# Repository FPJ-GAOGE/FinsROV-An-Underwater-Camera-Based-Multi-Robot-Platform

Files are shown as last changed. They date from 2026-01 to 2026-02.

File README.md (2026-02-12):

## FinsROV: an Underwater Camera-Based Multi-robot platform





FinsROV is a low-cost, open-source Underwater robot platform designed for underwater task and research in robotics and AI. The eight-thruster configuration effectively ensures the flexibility of the robot's omnidirectional movement, and the dual-gimbal platform provides ample hardware expansion space, which can be applied to task scenarios such as underwater object tracking and underwater target recognition. This project supports both Chinese and English languages, though some videos and documents are only available in Chinese (Maybe this is a great opportunity to learn Chinese LOL)

FinsROV是一台开源的低成本水下机器人平台，面向AI和机器人领域中的水下任务和研究针对性设计。八推进器结构有效的保证了机器人全向运动的的灵活性，双云台平台提供了充足的硬件扩展空间，可以运用于水下物体跟踪，水下目标识别等任务场景。本项目提供中英两种语言的支持，但部分视频和文件仅有中文支持

## Overview

The FinsROV consists of a waterproof compartment with its internal circuitry, 8 propellers, 4 servos, 4 water depth sensors, and various brackets in total, with the model shown as follows:

FinsROV整体包含防水仓及其内部电路、推进器 x8、舵机 x4、水深传感器 x4以及各个支架，模型如下：
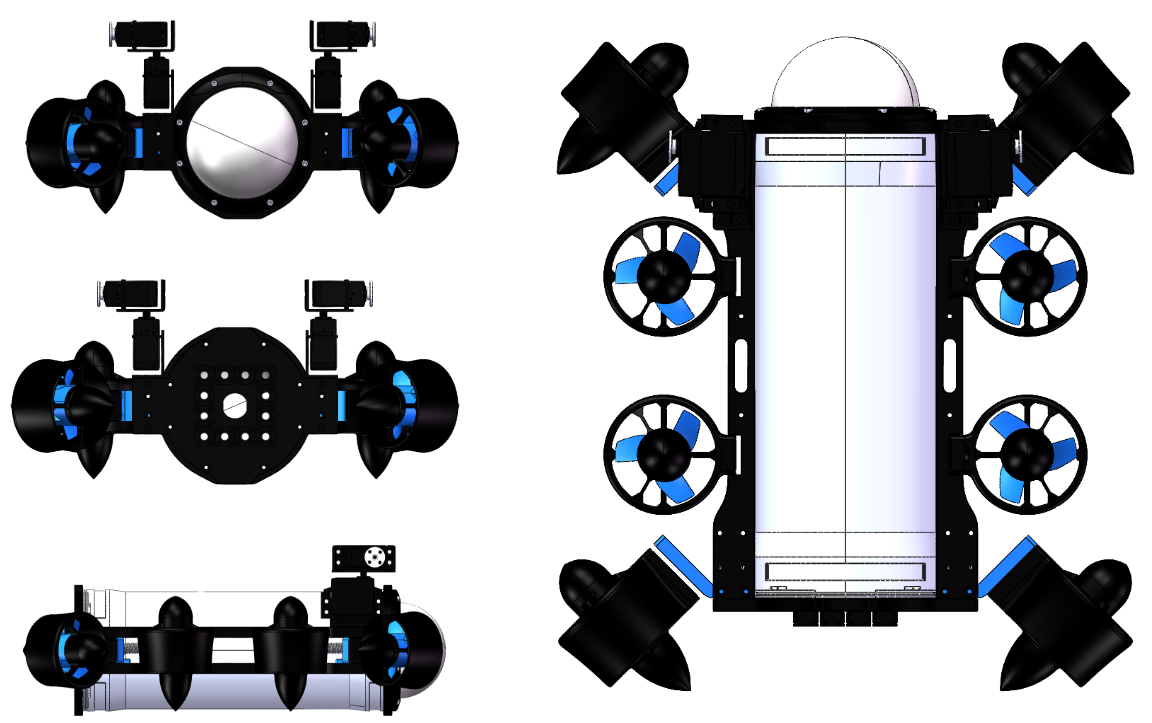
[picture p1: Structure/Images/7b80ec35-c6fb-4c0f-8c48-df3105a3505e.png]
Model


FinsROV is equipped with two 2-DOF gimbals mounted on either side of the submersible respectively. Each gimbal consists of two servos, with a maximum rotation angle of -90° to 90° for each servo.

FinsROV配置了两个二自由度的云台、分别置于潜器的两侧，一个云台由两个舵机组成，每个舵机的最大旋转角度为（-90°~90°）


We have open-sourced all structural components of the underwater robot, which can be found in the [Structure](https://github.com/FPJ-GAOGE/FinsROV-An-Underwater-Camera-Based-Multi-Robot-Platform/tree/main/Structure) folder, with the corresponding STEP files provided. The robot’s structure can be modified using software such as Solidworks, and the relevant structural components can be manufactured by means including 3D printing and CNC machining. We welcome everyone to upgrade and modify this robot platform.

我们开源了水下机器人所有的结构件，在[Structure](https://github.com/FPJ-GAOGE/FinsROV-An-Underwater-Camera-Based-Multi-Robot-Platform/tree/main/Structure)文件夹中，提供对应的STEP文件，通过Solidworks等软件，可以对机器人结构进行修改。通过3D打印或者CNC加工等不同的形式，都可以制造对应的结构件，我们欢迎大家对机器人平台进行升级和改造

## Parameters

<table style="width:100%; border-collapse: collapse;">
  <thead>
    <tr style="border: 1px solid #ddd;">
      <th style="border: 1px solid #ddd; padding: 8px; text-align: left;">Category</th>
      <th style="border: 1px solid #ddd; padding: 8px; text-align: left;">Sub-item</th>
      <th style="border: 1px solid #ddd; padding: 8px; text-align: left;">Parameter</th>
      <th style="border: 1px solid #ddd; padding: 8px; text-align: left;">Supplementary Note</th>
    </tr>
  </thead>
  <tbody>
    <tr style="border: 1px solid #ddd;">
      <td rowspan="4" style="border: 1px solid #ddd; padding: 8px; background-color: #f5f5f5;"><strong>Specifications</strong></td>
      <td style="border: 1px solid #ddd; padding: 8px;">Dimensions (Length × Width × Height)</td>
      <td style="border: 1px solid #ddd; padding: 8px;">40cm*35cm*15cm</td>
      <td style="border: 1px solid #ddd; padding: 8px;">-</td>
    </tr>
    <tr style="border: 1px solid #ddd;">
      <td style="border: 1px solid #ddd; padding: 8px;">Power & Endurance Time</td>
      <td style="border: 1px solid #ddd; padding: 8px;">Approx. 13.75W, Approx. 2h</td>
      <td style="border: 1px solid #ddd; padding: 8px;">Adapted to RC model batteries with xt30/60 interface</td>
    </tr>
    <tr style="border: 1px solid #ddd;">
      <td style="border: 1px solid #ddd; padding: 8px;">Weight in Air</td>
      <td style="border: 1px solid #ddd; padding: 8px;">4.85Kg</td>
      <td style="border: 1px solid #ddd; padding: 8px;">-</td>
    </tr>
    <tr style="border: 1px solid #ddd;">
      <td style="border: 1px solid #ddd; padding: 8px;">Operating Depth</td>
      <td style="border: 1px solid #ddd; padding: 8px;">10-20m (Passed internal pressure test)</td>
      <td style="border: 1px solid #ddd; padding: 8px;">Passed internal pressure test</td>
    </tr>
    <tr style="border: 1px solid #ddd;">
      <td rowspan="6" style="border: 1px solid #ddd; padding: 8px; background-color: #f5f5f5;"><strong>Power System</strong></td>
      <td style="border: 1px solid #ddd; padding: 8px;">Maximum Acceleration in Still Water</td>
      <td style="border: 1px solid #ddd; padding: 8px;">4.6m/s²</td>
      <td style="border: 1px solid #ddd; padding: 8px;">-</td>
    </tr>
    <tr style="border: 1px solid #ddd;">
      <td style="border: 1px solid #ddd; padding: 8px;">Maximum Speed in Still Water</td>
      <td style="border: 1px solid #ddd; padding: 8px;">Approx. 3m/s</td>
      <td style="border: 1px solid #ddd; padding: 8px;">-</td>
    </tr>
    <tr style="border: 1px solid #ddd;">
      <td style="border: 1px solid #ddd; padding: 8px;">Maximum Angular Velocity of Steering in Still Water</td>
      <td style="border: 1px solid #ddd; padding: 8px;">5.7rad/s</td>
      <td style="border: 1px solid #ddd; padding: 8px;">-</td>
    </tr>
    <tr style="border: 1px solid #ddd;">
      <td style="border: 1px solid #ddd; padding: 8px;">Control Frequency</td>
      <td style="border: 1px solid #ddd; padding: 8px;">150Hz</td>
      <td style="border: 1px solid #ddd; padding: 8px;">Can be adjusted according to actual needs</td>
    </tr>
    <tr style="border: 1px solid #ddd;">
      <td style="border: 1px solid #ddd; padding: 8px;">Baud Rate</td>
      <td style="border: 1px solid #ddd; padding: 8px;">115200</td>
      <td style="border: 1px solid #ddd; padding: 8px;">-</td>
    </tr>
    <tr style="border: 1px solid #ddd;">
      <td style="border: 1px solid #ddd; padding: 8px;">Load Capacity</td>
      <td style="border: 1px solid #ddd; padding: 8px;">10-15N</td>
      <td style="border: 1px solid #ddd; padding: 8px;">-</td>
    </tr>
  </tbody>
</table>

<table style="width:100%; border-collapse: collapse;">
  <thead>
    <tr style="border: 1px solid #ddd;">
      <th style="border: 1px solid #ddd; padding: 8px; text-align: left;">类别</th>
      <th style="border: 1px solid #ddd; padding: 8px; text-align: left;">子项</th>
      <th style="border: 1px solid #ddd; padding: 8px; text-align: left;">参数</th>
      <th style="border: 1px solid #ddd; padding: 8px; text-align: left;">补充说明</th>
    </tr>
  </thead>
  <tbody>
    <tr style="border: 1px solid #ddd;">
      <td rowspan="4" style="border: 1px solid #ddd; padding: 8px; background-color: #f5f5f5;"><strong>规格</strong></td>
      <td style="border: 1px solid #ddd; padding: 8px;">尺寸（长×宽×高）</td>
      <td style="border: 1px solid #ddd; padding: 8px;">40cm*35cm*15cm</td>
      <td style="border: 1px solid #ddd; padding: 8px;"></td>
    </tr>
    <tr style="border: 1px solid #ddd;">
      <td style="border: 1px solid #ddd; padding: 8px;">功率 续航时间</td>
      <td style="border: 1px solid #ddd; padding: 8px;">约13.75W，约2h</td>
      <td style="border: 1px solid #ddd; padding: 8px;">适配xt30/60接口的航模电池</td>
    </tr>
    <tr style="border: 1px solid #ddd;">
      <td style="border: 1px solid #ddd; padding: 8px;">空气中重量</td>
      <td style="border: 1px solid #ddd; padding: 8px;">4.85Kg</td>
      <td style="border: 1px solid #ddd; padding: 8px;"></td>
    </tr>
    <tr style="border: 1px solid #ddd;">
      <td style="border: 1px solid #ddd; padding: 8px;">作业深度</td>
      <td style="border: 1px solid #ddd; padding: 8px;">10-20m，已通过内压测试</td>
      <td style="border: 1px solid #ddd; padding: 8px;">已通过内压测试</td>
    </tr>
    <tr style="border: 1px solid #ddd;">
      <td rowspan="6" style="border: 1px solid #ddd; padding: 8px; background-color: #f5f5f5;"><strong>动力系统</strong></td>
      <td style="border: 1px solid #ddd; padding: 8px;">静水航行最大加速度</td>
      <td style="border: 1px solid #ddd; padding: 8px;">4.6m/s^2</td>
      <td style="border: 1px solid #ddd; padding: 8px;"></td>
    </tr>
    <tr style="border: 1px solid #ddd;">
      <td style="border: 1px solid #ddd; padding: 8px;">静水航行最大速度</td>
      <td style="border: 1px solid #ddd; padding: 8px;">约3m/s</td>
      <td style="border: 1px solid #ddd; padding: 8px;"></td>
    </tr>
    <tr style="border: 1px solid #ddd;">
      <td style="border: 1px solid #ddd; padding: 8px;">静水转向最大角速度</td>
      <td style="border: 1px solid #ddd; padding: 8px;">5.7rad/s</td>
      <td style="border: 1px solid #ddd; padding: 8px;"></td>
    </tr>
    <tr style="border: 1px solid #ddd;">
      <td style="border: 1px solid #ddd; padding: 8px;">控制频率</td>
      <td style="border: 1px solid #ddd; padding: 8px;">150Hz</td>
      <td style="border: 1px solid #ddd; padding: 8px;">可以根据实际需要进行调整</td>
    </tr>
    <tr style="border: 1px solid #ddd;">
      <td style="border: 1px solid #ddd; padding: 8px;">波特率</td>
      <td style="border: 1px solid #ddd; padding: 8px;">115200</td>
      <td style="border: 1px solid #ddd; padding: 8px;"></td>
    </tr>
    <tr style="border: 1px solid #ddd;">
      <td style="border: 1px solid #ddd; padding: 8px;">载荷</td>
      <td style="border: 1px solid #ddd; padding: 8px;">10-15N</td>
      <td style="border: 1px solid #ddd; padding: 8px;"></td>
    </tr>
  </tbody>
</table>

## BOM

The complete BOM of our robot is shown below. For regions where components can be directly purchased on Taobao, you may click the links directly (this is not an advertisement; you may purchase from other suppliers). For those with no access to Taobao, please refer to the following information. A downloadable version of the BOM is also available in the Structure folder.

我们机器人的完整BOM表格如下，对于能够直接通过淘宝采购零部件的地区，可以直接点击链接参考（不涉及任何广告，仅供参考）。在Structure文件中也有对应可下载的BOM文件。

[中文版本](https://docs.google.com/spreadsheets/d/1fIgdKPsx-9QTdMGvk-Vg6hmxgAVsjg4v-JMBh90Yp5g/edit?gid=0#gid=0)

[English Version BOM](https://docs.google.com/spreadsheets/d/1fIgdKPsx-9QTdMGvk-Vg6hmxgAVsjg4v-JMBh90Yp5g/edit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)

## Controller

All controller codes are stored in the [Lower level controller](https://github.com/FPJ-GAOGE/FinsROV-An-Underwater-Camera-Based-Multi-Robot-Platform/tree/main/Code/Lower_Level_Controller) and can be used with the Readme file. In this project, our lower-level controller is based on the DJI Robomaster C-board (STM32F4) and developed with Keil. For secondary development of the code, you need to download Keil Version 5.38 or later, and it depends on the file Keil.STM32F4xx_DFP.2.14.0.pack. Install dpinst_x86.exe (for 32-bit systems) or dpinst_amd64.exe (for 64-bit systems) from the STLink package. The process for wireless programmers is similar to that of wired programmers; simply select CMSIS-DAP Debugger when choosing the debug tool, and there is generally no need to modify the clock frequency. For better performance, we recommend using the [FINEMOTE](https://github.com/FINS-Fines/FineMote) developed by our laboratory (note: some hardware is not yet adapted). It is a powerful embedded development framework that will also be used synchronously in our new-generation underwater robots.

控制器代码在[Lower level controller](https://github.com/FPJ-GAOGE/FinsROV-An-Underwater-Camera-Based-Multi-Robot-Platform/tree/main/Code/Lower_Level_Controller)文件夹中，配合Readme使用，本项目中我们的下位机是基于DJI Robomaster C板（STM32F4），使用Keil进行开发的。如果需要对代码进行二次开发，需要下载Keil 5.38以上版本。依赖Keil.STM32F4xx_DFP.2.14.0.pack文件。安装stlink中的dpinst_x86.exe（32位）或 dpinst_amd64.exe（64位）。无线烧写器与有线烧写器流程类似，在选择调试工具的时候改为选择CMSIS-DAP Debugger即可，一般不需要修改时钟频率。如果你想有更好的性能，推荐使用我们实验室开发的[FINEMOTE框架](https://github.com/FINS-Fines/FineMote)（部分硬件暂未适配），这是一种强大的嵌入式开发框架，我们新一代的水下机器人上也会同步使用该框架

## Wired-Joystick

Our robot platform supports a variety of host computer systems, including but not limited to Windows, Linux, macOS, Android, Raspberry Pi, etc. We recommend using a game Joystick for control. The relevant code is available in [Joystick_Control](https://github.com/FPJ-GAOGE/FinsROV-An-Underwater-Camera-Based-Multi-Robot-Platform/tree/main/Code/Joystick_Control) and should be used in conjunction with the Readme file.

我们的机器人平台支持多种上位机系统，包括但不限于windows，linux，Mac os，Android，树莓派等，我们推荐使用手柄进行控制。相关代码在[Joystick_Control](https://github.com/FPJ-GAOGE/FinsROV-An-Underwater-Camera-Based-Multi-Robot-Platform/tree/main/Code/Joystick_Control)中，配合Readme使用

## Education

We provide a complete set of video tutorials for building the underwater vehicle. We sincerely apologize that these tutorials are only available on Bilibili with Chinese voice-overs and subtitles. We will also upload other relevant content, and we welcome you to subscribe to our [channel](https://space.bilibili.com/1188256336?spm_id_from=333.40164.0.0). Additionally, the [Making_Instructions](https://github.com/FPJ-GAOGE/FinsROV-An-Underwater-Camera-Based-Multi-Robot-Platform/tree/main/Making_Instructions) folder also contains some documentation on the making instructions.

我们为制作潜器提供完整的视频教程，但是非常抱歉，相关教程上传至BiliBili且只有中文配音与字幕。我们也会上传其他相关的内容，[欢迎订阅](https://space.bilibili.com/1188256336?spm_id_from=333.40164.0.0)。同时，[Making_Instructions](https://github.com/FPJ-GAOGE/FinsROV-An-Underwater-Camera-Based-Multi-Robot-Platform/tree/main/Making_Instructions)中也包含部分制作说明文档。

How to bulid the robot platform & coding: [【上海交通大学】从0-1带你制作水下机器人](https://www.bilibili.com/video/BV13vcvzgEv3?p=11&vd_source=225e86b359e69725bfc871c2685a31c8)

Basic theory about underwater robot: [【面向水下机器人的动力学与运动学建模及控制器分析】](https://www.bilibili.com/video/BV1VXmQBRE2a/?share_source=copy_web&vd_source=898a23397484d4386766c76dfa58679f)

Demo: [【目前可公开的情报：FINS第一代水下机器人】](https://www.bilibili.com/video/BV1oC41177Rn/?share_source=copy_web&vd_source=e6237e17b71511df8920049cd998c076)

## Thank & Citation

This project acknowledges the contributions of Ding Lin, Jisheng Xu, Jiahao Lin, Yanqi Feng, Jiaming Guo and other students who are or have been part of the FINS-Underwater Group.

这个项目要感谢Ding Lin, Jisheng Xu, Jiahao Lin, Yanqi Feng, Jiaming Guo等来自或参与过FINS-Underwater Group的同学的贡献 

If you find this code useful, we would appreciate if you would cite our paper:

如果你觉得我们的开源项目能够帮助到你，欢迎你引用我们的文章！并持续关注我们的后续研究：
```
@article{xu2025aucamp,
  title={Aucamp: An Underwater Camera-Based Multi-Robot Platform with Low-Cost, Distributed, and Robust Localization},
  author={Xu, Jisheng and Lin, Ding and Fong, Pangkit and Fang, Chongrong and Duan, Xiaoming and He, Jianping},
  journal={arXiv preprint arXiv:2506.09876},
  year={2025}
}
```

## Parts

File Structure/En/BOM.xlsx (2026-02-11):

Type | Item Description | Link | Detail | Price(CNY) | Number | Note
Disclaimer | We are not affiliated with or endorse this company in any way. We have not tested or validated the product. Any such offerings are independent of our project.
 | If you are from regions outside mainland China or areas where Taobao e-commerce services are not readily available, you may refer to the BOM specifications to purchase equivalent items through convenient channels, but we cannot guarantee the consistency of the final assembly results. |  |  |  |  |  | The quantity of screws is for reference only; please prepare extra ones.
Essentials
Structure | Rear cabin hatch |  | Custom Aluminum Alloy CNC Machining | 240 | 1 |  | Category | Type | Number
 | Front cabin mount |  |  | 180 | 1 |  | Countersunk Head Hexagon Socket Screw | M3(Head Diameter6)*5 | 20
 | Thruster mount |  |  | 680 | 4 |  |  | M3(Head Diameter6)*10 | 8
 | Horizontal thruster bracket |  |  | 480 | 4 |  |  | M3(Head Diameter8)*8 | 16
 | Cable-passing screw |  |  | 1140 | 12 |  | Cup Head Hexagon Socket Screw | M4*16 | 32
 | Underwater aviation connector | https://item.taobao.com/item.htm?spm=a1z09.2.0.0.18002e8dzucueB&id=619481441943&_u=f2ig9se45843 | 3W 6-Core | 272 | 1 | Send cable directly to supplier for processing. |  | M3*16 | 20
 | Servo connector | https://item.taobao.com/item.htm?id=557166026079&sku_properties=31309:48651884 | Multifunctional Bracket | 18.4 | 4 |  |  | M3*12 | 45
 |  |  | Metal Servo Horn | 10 | 4 |  |  | M3*10 | 8
 | Waterproof compartment | https://item.taobao.com/item.htm?spm=a1z09.2.0.0.ef7d2e8dO2XjuV&id=662343463249&_u=92ig9se46f55 | Cabin Tube & Flange Kit + Hemispherical Cover + Pressure Plate | 515 | 1 |  |  | M2.5*8 | 4
 | Internal bracket of waterproof compartment | 3D打印 |  |  |  |  |  | M2*10 | 48
Electronics | Propeller | https://item.taobao.com/item.htm?spm=a1z09.2.0.0.ef7d2e8dO2XjuV&id=591864716045&_u=92ig9se435ad | 1 Pair of CW/CCW Propellers (Built-in ESC for 4S Voltage) | 2037 | 4 |  |  | M3*4 | 12
 | Servo | LIEYING/QFS2025全防水/潜水/水下机器人舵机全金属外壳IPX68等级-淘宝网 (taobao.com) (https://item.taobao.com/item.htm?_u=i20at7545jacc4&id=680656749408&spm=a1z09.2.0.0.3c6c2e8dmFwRSe) | 20KG (for Underwater Diving) Underwater Robot, 180° (0.5-2.5ms) | 432 | 4 | Custom extended cable, total length 1m. |  | M2.5*4 | 4
 | Water depth sensor | M10 水压水深传感器 高精度 深度传感器 MS5837-30BA 带温度 ROV-淘宝网 (taobao.com) (https://item.taobao.com/item.htm?_u=320at7545j5b4a&id=605375059849&spm=a1z09.2.0.0.2d472e8d3f5Wg1) | Standard Version, Stainless Steel, 10m, Sensor Adapter Board Kit | 1319.6 | 4 | Custom extended cable, total length 60cm. | Single-head Copper Spacer | M3*4+4 | 12
 | I2C expansion board | TCA9548A IIC多路扩展模块 8路I2C通信 I2C开关开发-淘宝网 (https://item.taobao.com/item.htm?id=677595693967&skuId=6126765579570) | Straight/Right-Angle Pin Headers | 10.56 | 1 |  |  | M2.5*4+4 | 4
 | PWM expansion board | 16路PWM Servo 舵机驱动板机器人控制器IIC接口驱动器模块PCA9685-tmall.com天猫 (https://detail.tmall.com/item.htm?_u=m20at7545j0770&id=624960039615&spm=a1z09.2.0.0.570d2e8dWadFaY) | Pre-Soldered | 15 | 1 |  | Hexagonal Single-head Nylon Spacer | M3*70+6 | 6
 | TTL to 422 converter | RS422互转TTL双向信号 全双工422转单片机MAX490转TTL模块-tmall.com天猫 (https://detail.tmall.com/item.htm?_u=q2ig9se4d19b&id=715839278393) |  | 9.1 | 1 |  |  | M3*45+6 | 3
 | 422 to USB converter | 绿联usb转rs485/422/232串口线工业级九针db9针数据调试接口通讯模块芯片连接笔记本和电脑口转接头转换器-tmall.com天猫 (https://detail.tmall.com/item.htm?id=599997955029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) | 1 Piece, Length Customizable | 79 | 1 |  |  | M3*40+6 | 3
 | Wireless debugger | 高速无线调试器DAPLink仿真器STM32编程烧录下载器塔克OpenCTR-淘宝网 (https://item.taobao.com/item.htm?abbucket=8&id=745548099223&ns=1&skuId=5310177214467&xxc=taobaoSearch) | 2 Debuggers + Dupont Cables | 89 | 2 |  | Cap Nut | M3 | 16
 | DJI RoboMaster C-board | ROBOMASTER萝马集市 开发板C型-淘宝网 (taobao.com) (https://item.taobao.com/item.htm?_u=i20at7545j5174&id=611226266955&spm=a1z09.2.0.0.292e2e8d43HZbM) |  | 379 | 1 |  | Hex Nut | M3 | 4
 | Camera |  | Either External Waterproof Camera or Internal Cabin Camera is Acceptable |  | 1 |  | Embedded Nut | M3*4+6 | 4
Others | Cable |  | Custom Zero-Buoyancy Cable: 2p*1mm² Power Cable + 4p Signal Cable
 | Screw |  | See the right table
 | Terminal block | https://item.taobao.com/item.htm?id=562191894078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 | h3802 10P | 25.2 | 2
 |  |  | Chocolate Color [EBL-10-5-Connector], Non-printed | 12.6 | 2
 |  | https://item.taobao.com/item.htm?spm=a1z09.2.0.0.5b912e8dQl5wtC&id=661948958655&_u=h2ig9se4f606 | h3800 12P | 36 | 2
 |  |  | h3800 16P | 24 | 1
 | Terminal block
 | Dupont adapter cable |  | 4P 100mm to Dupont Female SH1.25; 3P 100mm to Dupont Female GH1.25
 | Dupont cable |  | 6-Color Male to Female, 10cm
 | Waterproof gasket | 绿色氟胶O型圈外10.5/11/11.5/12/12.5/13/13.5/14/14.5/15*1.5mm-tmall.com天猫 (https://detail.tmall.com/item.htm?id=680012535670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) | Outer Diameter 12mm*1.5mm |  | 12

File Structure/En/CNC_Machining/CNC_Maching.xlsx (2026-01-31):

Name | Quantity | Material | Remarks
Front_Cabin_Mount | 1 | Al Alloy Anodized Black
Rear_Cabin_Hatch | 1 | Al Alloy Anodized Black | All similar locations here: drill & tap M2 threaded holes, depth 4 mm, Qty. 48
Thruster_Mount | 4 | Al Alloy Anodized Black | All similar locations here: drill & tap M3 threaded holes, depth 10 mm, Qty. 12
Horizontal_Thruster_Bracket | 4 | Al Alloy Anodized Blue | All similar locations here: drill & tap M3 threaded holes, depth 8 mm, Qty. 6
Cable-passing_Screw | 12 | Al Alloy Anodized Black

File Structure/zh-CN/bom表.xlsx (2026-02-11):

类别 | 材料名称 | 购买链接 | 型号 | 价格 | 数量 | 备注
声明 | 本表格不涉及任何广告，物料均为机器人标准件，我方与店家无任何关联，亦未对其进行背书。我方尚未对该产品开展测试或验证工作，相关产品服务均独立于本项目存在
 |  |  |  |  |  |  | 螺丝数量仅供参考，请多预备
核心配件清单
机械零件 | 后密封舱盖支撑 |  | 铝合金CNC定制 | 240 | 1 |  | 螺丝种类 | 型号 | 数量
 | 前密封舱支撑 |  |  | 180 | 1 |  | 扁头内六角螺丝 | M3(头径6)*5 | 20
 | 推进器支撑 |  |  | 680 | 4 |  |  | M3(头径6)*10 | 8
 | 水平推进器架 |  |  | 480 | 4 |  |  | M3(头径8)*8 | 16
 | 穿线螺丝 |  |  | 1140 | 12 |  | 杯头内六角螺丝 | M4*16 | 32
 | 水下航插 | https://item.taobao.com/item.htm?spm=a1z09.2.0.0.18002e8dzucueB&id=619481441943&_u=f2ig9se45843 | 3W 6芯 | 272 | 1 | 可以将电缆直接寄给商家加工 |  | M3*16 | 20
 | 舵机连接件 | https://item.taobao.com/item.htm?id=557166026079&sku_properties=31309:48651884 | 多功能支架 | 18.4 | 4 |  |  | M3*12 | 45
 |  |  | 金属舵盘 | 10 | 4 |  |  | M3*10 | 8
 | 防水舱 | https://item.taobao.com/item.htm?spm=a1z09.2.0.0.ef7d2e8dO2XjuV&id=662343463249&_u=92ig9se46f55 | 舱管和法兰套装+ 半球罩+压板 | 515 | 1 |  |  | M2.5*8 | 4
 | 防水舱内部支架 | 3D打印 |  |  |  |  |  | M2*10 | 48
电气设备 | 推进器 | https://item.taobao.com/item.htm?spm=a1z09.2.0.0.ef7d2e8dO2XjuV&id=591864716045&_u=92ig9se435ad | 正反桨（4S电压内置电调）一对（开票价） | 2037 | 4 |  |  | M3*4 | 12
 | 舵机 | LIEYING/QFS2025全防水/潜水/水下机器人舵机全金属外壳IPX68等级-淘宝网 (taobao.com) (https://item.taobao.com/item.htm?_u=i20at7545jacc4&id=680656749408&spm=a1z09.2.0.0.3c6c2e8dmFwRSe) | 20KG（水下潜水用）水下机器人 180度（0.5-2.5ms） | 432 | 4 | 需要定制加长线，总长1m |  | M2.5*4 | 4
 | 水深传感器 | M10 水压水深传感器 高精度 深度传感器 MS5837-30BA 带温度 ROV-淘宝网 (taobao.com) (https://item.taobao.com/item.htm?_u=320at7545j5b4a&id=605375059849&spm=a1z09.2.0.0.2d472e8d3f5Wg1) | 标准版 不锈钢 10m 传感器转接板套装 | 1319.6 | 4 | 需要定制加长线，总长60cm | 单头铜柱 | M3*4+4 | 12
 | IIC扩展板 | TCA9548A IIC多路扩展模块 8路I2C通信 I2C开关开发-淘宝网 (https://item.taobao.com/item.htm?id=677595693967&skuId=6126765579570) | 直/弯排针 | 10.56 | 1 |  |  | M2.5*4+4 | 4
 | PWM扩展板 | 16路PWM Servo 舵机驱动板机器人控制器IIC接口驱动器模块PCA9685-tmall.com天猫 (https://detail.tmall.com/item.htm?_u=m20at7545j0770&id=624960039615&spm=a1z09.2.0.0.570d2e8dWadFaY) | 焊好 | 15 | 1 |  | 六角单头尼龙柱 | M3*70+6 | 6
 | TTL转422 | RS422互转TTL双向信号 全双工422转单片机MAX490转TTL模块-tmall.com天猫 (https://detail.tmall.com/item.htm?_u=q2ig9se4d19b&id=715839278393) |  | 9.1 | 1 |  |  | M3*45+6 | 3
 | 422转USB | 绿联usb转rs485/422/232串口线工业级九针db9针数据调试接口通讯模块芯片连接笔记本和电脑口转接头转换器-tmall.com天猫 (https://detail.tmall.com/item.htm?id=599997955029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) | 1条，长度自选 | 79 | 1 |  |  | M3*40+6 | 3
 | 无线调试器 | 高速无线调试器DAPLink仿真器STM32编程烧录下载器塔克OpenCTR-淘宝网 (https://item.taobao.com/item.htm?abbucket=8&id=745548099223&ns=1&skuId=5310177214467&xxc=taobaoSearch) | 两个调试器+杜邦线 | 89 | 2 |  | 盖形螺母 | M3 | 16
 | 大疆RM C板 | ROBOMASTER萝马集市 开发板C型-淘宝网 (taobao.com) (https://item.taobao.com/item.htm?_u=i20at7545j5174&id=611226266955&spm=a1z09.2.0.0.292e2e8d43HZbM) |  | 379 | 1 |  | 六角螺母 | M3 | 4
 | 相机 |  | 外置防水相机或者舱内相机都可以 |  | 1 |  | 预埋螺母 | M3*4+6 | 4
其他 | 电缆 |  | 定制零浮力电缆 2p*1mm^2电源线+4p信号线 |  |  | 按需求定制长度 |  | M3*4+4 | 14
 | 螺丝 |  | 见右侧 |  |  |  |  | M2.5*3.5+4 | 4
 | 接线端子 | https://item.taobao.com/item.htm?id=562191894078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 | h3802 10p | 25.2 | 2
 |  |  | 巧克力色[EBL-10-5-连接件]不印字 | 12.6 | 2
 |  | https://item.taobao.com/item.htm?spm=a1z09.2.0.0.5b912e8dQl5wtC&id=661948958655&_u=h2ig9se4f606 | h3800 12p | 36 | 2
 |  |  | h3800 16p | 24 | 1
 | 接线端子
 | 杜邦转接线 |  | 4p100mm转杜邦母sh1.25 3p100mm转杜邦母gh1.25
 | 杜邦线 |  | 六色公对母10cm
 | 防水垫圈 | 绿色氟胶O型圈外10.5/11/11.5/12/12.5/13/13.5/14/14.5/15*1.5mm-tmall.com天猫 (https://detail.tmall.com/item.htm?id=680012535670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) | 外径12mm*1.5mm |  | 12

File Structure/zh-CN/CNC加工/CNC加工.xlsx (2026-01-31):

名称 | 数量 | 材料 | 备注
前密封舱支撑 | 1 | 铝合金，氧化黑
后密封舱盖 | 1 | 铝合金，氧化黑 | 此处所有类似地方需要做成m2螺纹孔，深4mm，共48个
推进器支撑 | 4 | 铝合金，氧化黑 | 此处需要做成m3螺纹孔，共12个
水平推进器架 | 4 | 铝合金，氧化蓝 | 此处需要做成m3螺纹孔，共6个
穿线螺丝M8 | 12 | 铝合金，氧化黑

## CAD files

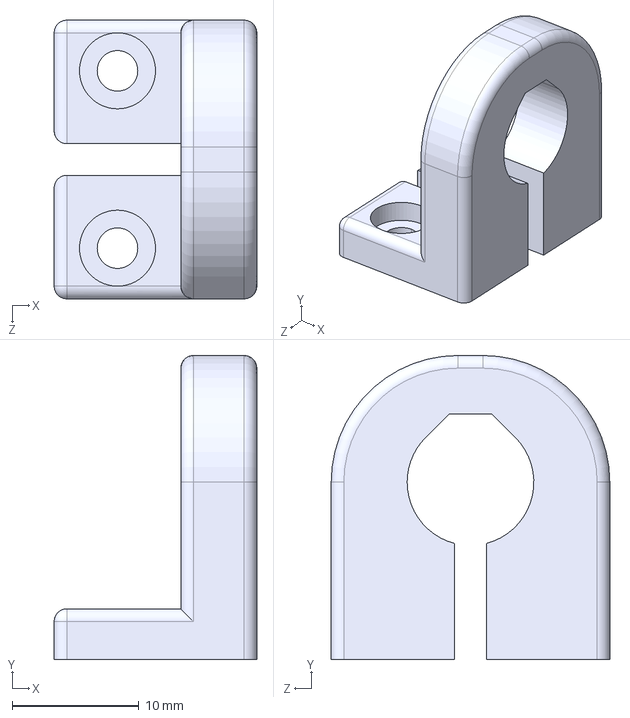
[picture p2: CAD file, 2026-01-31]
Structure/En/3DPrinting/Pressure_Sensor_Mount.STEP
16.0 x 24.0 x 22.0 mm

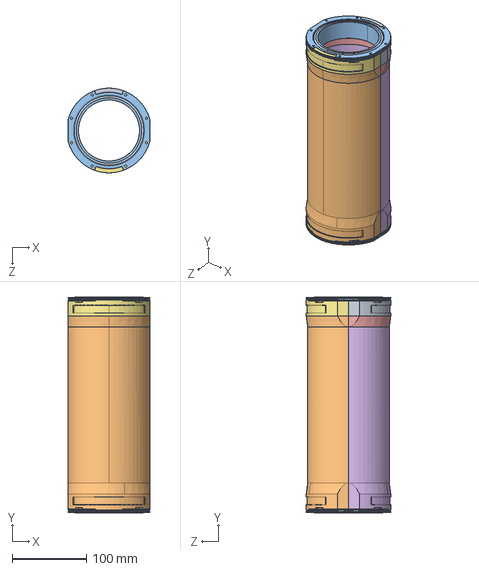
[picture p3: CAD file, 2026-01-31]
Structure/En/Cabin/Cabin.STEP
110.0 x 290.7 x 114.0 mm

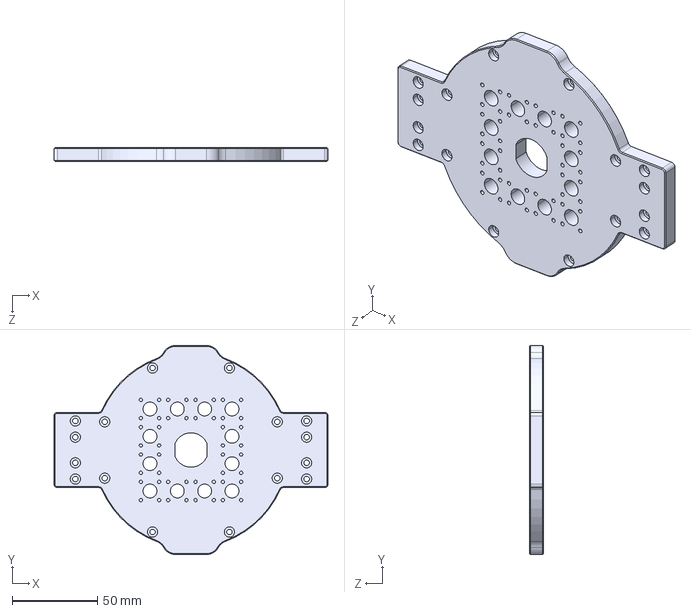
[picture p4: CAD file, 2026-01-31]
Structure/En/CNC_Machining/Rear_Cabin_Hatch.STEP
160.4 x 122.4 x 8.00 mm

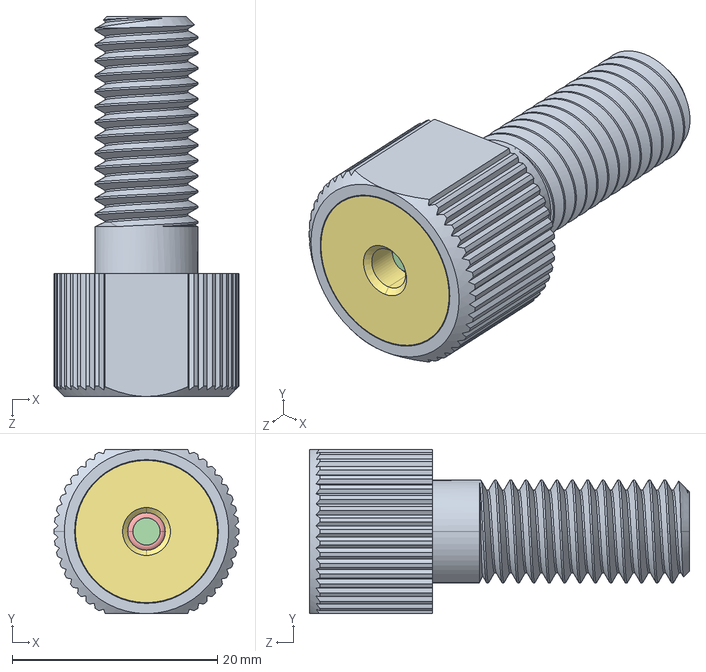
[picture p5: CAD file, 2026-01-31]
Structure/En/Pressure_Sensor/Pressure_Sensor.STEP
18.0 x 16.0 x 37.0 mm

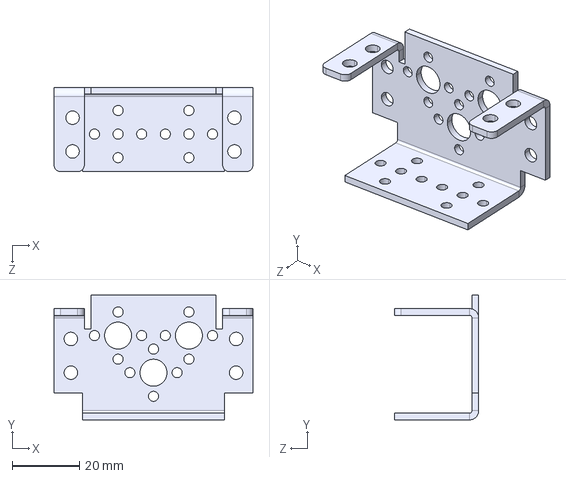
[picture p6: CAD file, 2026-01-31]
Structure/En/Servo/Servo_mount.STEP
59.0 x 37.0 x 25.0 mm

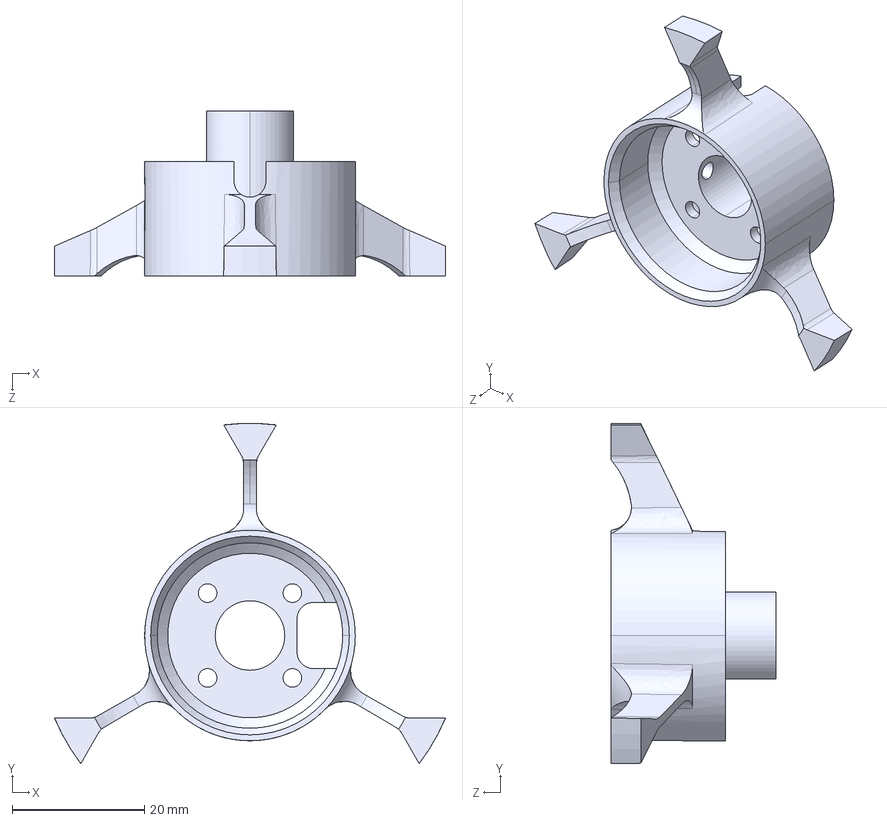
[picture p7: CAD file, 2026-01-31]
Structure/En/Thruster/YD11-24-3.stp.STEP
59.0 x 51.4 x 24.9 mm

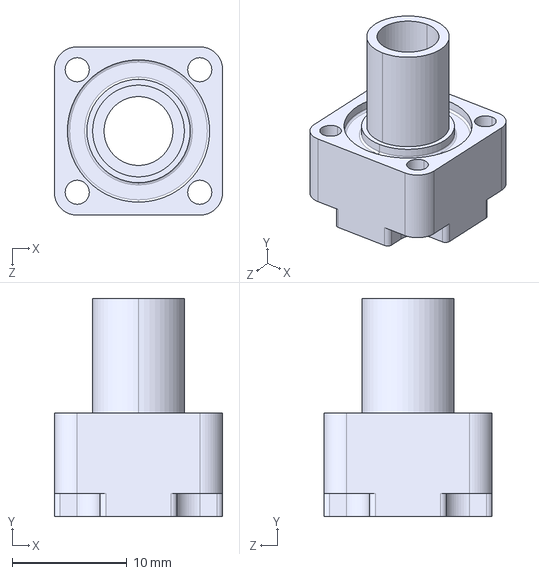
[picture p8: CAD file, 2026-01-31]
Structure/zh-CN/CNC加工/穿线螺丝M8.STEP
14.7 x 19.0 x 14.7 mm

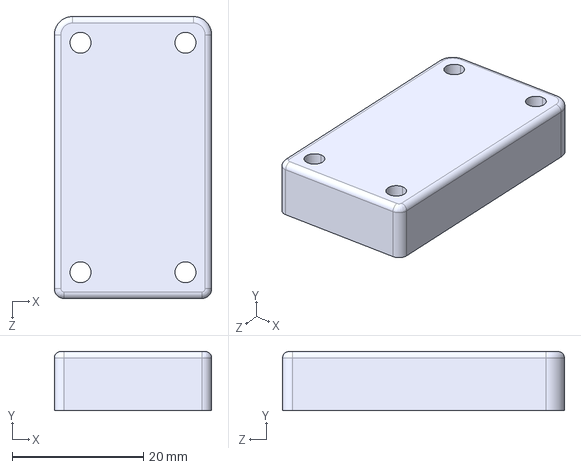
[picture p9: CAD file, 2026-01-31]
Structure/zh-CN/推进器/PRT0001.stp.STEP
24.0 x 9.00 x 43.0 mm

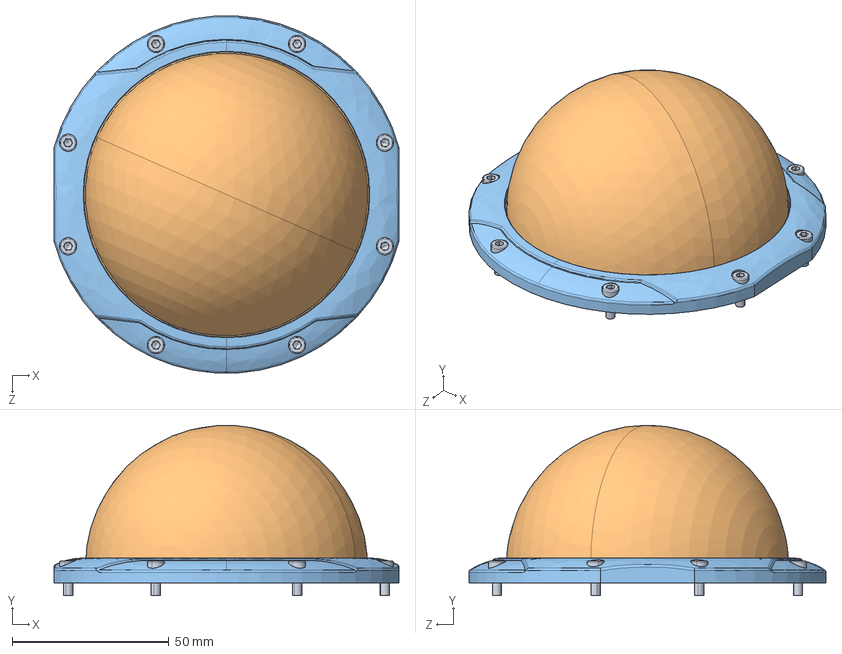
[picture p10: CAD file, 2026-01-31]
Structure/En/Cabin/Hemispherical_Dome.STEP
110.0 x 54.3 x 113.8 mm

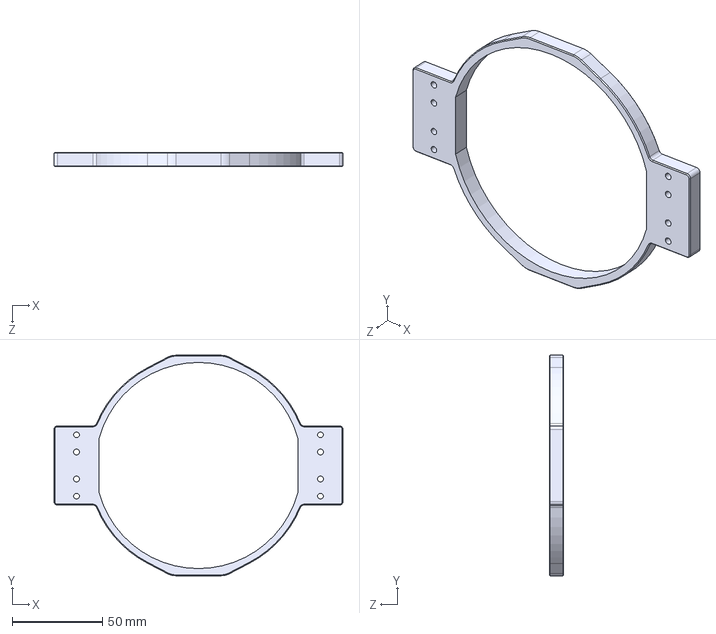
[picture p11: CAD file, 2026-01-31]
Structure/En/CNC_Machining/Front_Cabin_Mount.STEP
160.4 x 122.4 x 8.00 mm

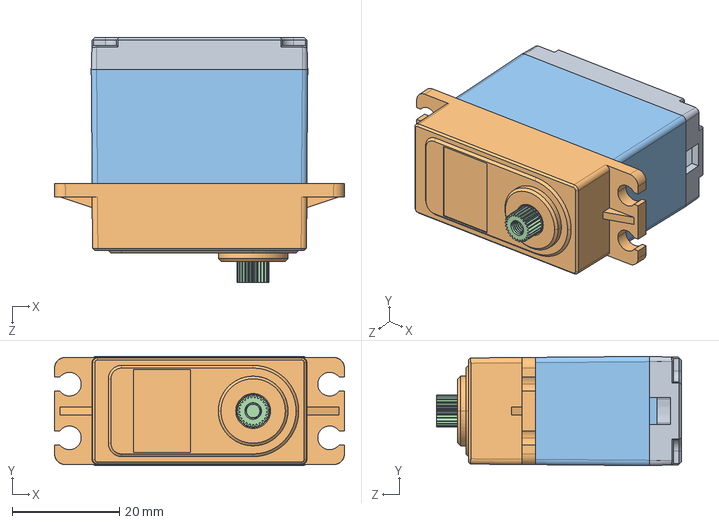
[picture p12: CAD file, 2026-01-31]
Structure/En/Servo/Servo.STEP
54.1 x 20.4 x 45.7 mm

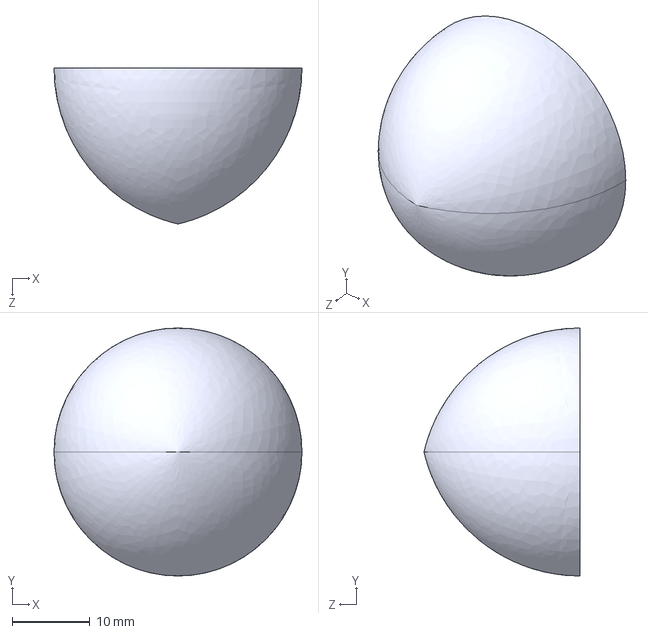
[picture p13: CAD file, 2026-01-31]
Structure/En/Thruster/YD11-24-1.stp.STEP
31.8 x 31.8 x 20.0 mm

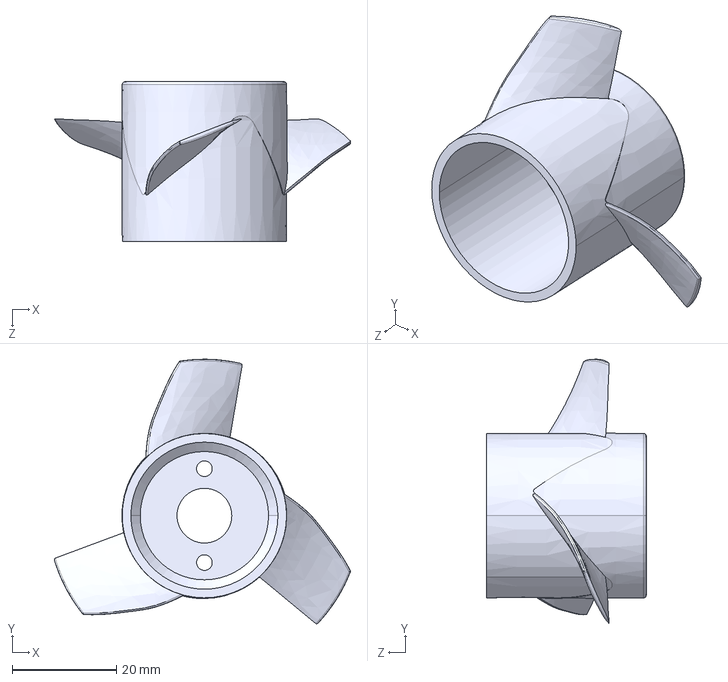
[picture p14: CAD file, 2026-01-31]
Structure/zh-CN/推进器/9-16-2.stp.STEP
56.8 x 50.7 x 30.6 mm

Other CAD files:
Structure/zh-CN/密封舱/密封舱.STEP
Structure/zh-CN/水深传感器/水深传感器架（3D打印）.STEP
Structure/zh-CN/舵机/舵机多功能支架.STEP
Structure/zh-CN/CNC加工/后密封舱盖.STEP
Structure/zh-CN/水深传感器/水深传感器.STEP
Structure/En/CNC_Machining/Cable-passing_Screw.STEP
Structure/En/CNC_Machining/Horizontal_Thruster_Bracket.STEP
Structure/En/CNC_Machining/Thruster_Mount.STEP
Structure/En/Servo/Servo_Horn.STEP
Structure/En/Thruster/9-16-2.stp.STEP
Structure/En/Thruster/PRT0001.stp.STEP
Structure/En/Thruster/Thruster.STEP
Structure/En/Thruster/YD11-24-2.stp.STEP
Structure/zh-CN/CNC加工/前密封舱支撑.STEP
Structure/zh-CN/CNC加工/推进器支撑.STEP
Structure/zh-CN/CNC加工/水平推进器架.STEP
Structure/zh-CN/推进器/YD11-24-1.stp.STEP
Structure/zh-CN/推进器/YD11-24-2.stp.STEP
Structure/zh-CN/推进器/YD11-24-3.stp.STEP
Structure/zh-CN/推进器/推进器.STEP
Structure/zh-CN/舵机/舵盘.STEP
Structure/zh-CN/舵机/防水舵机.STEP

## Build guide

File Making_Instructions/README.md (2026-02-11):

# Making Instructions
The waterproof compartment houses the basic circuitry for the submersible's operation, including 1 C-board, 1 I2C expansion board, 1 PWM expansion board, and the connecting wires for them. The waterproof compartment connects to external circuits via cable-passing screw holes on its back, with the connection corresponding to each screw hole as follows:

防水仓内包含了潜器运行的基本电路，包括C板 x1、IIC扩展板 x1、PWM扩展板 x1以及用于连接它们的电线。防水仓通过背部的穿线螺丝孔与外界电路进行连接，其中每个螺丝孔对应的连接为：

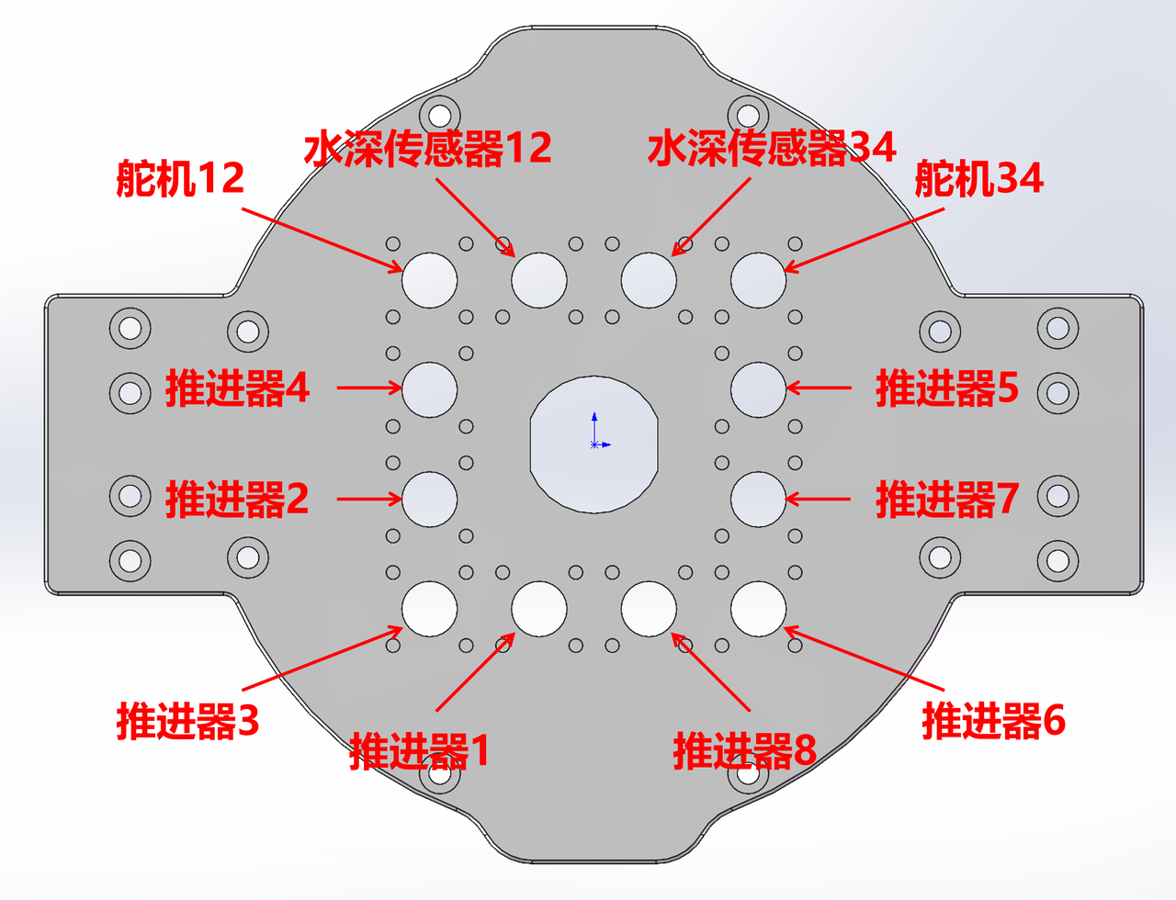
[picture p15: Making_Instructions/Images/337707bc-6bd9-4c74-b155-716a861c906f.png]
Wire


## Electronics
The complete wiring diagram for the robot's internal circuitry is shown below:

机器人内部电路的完整接线图如下：

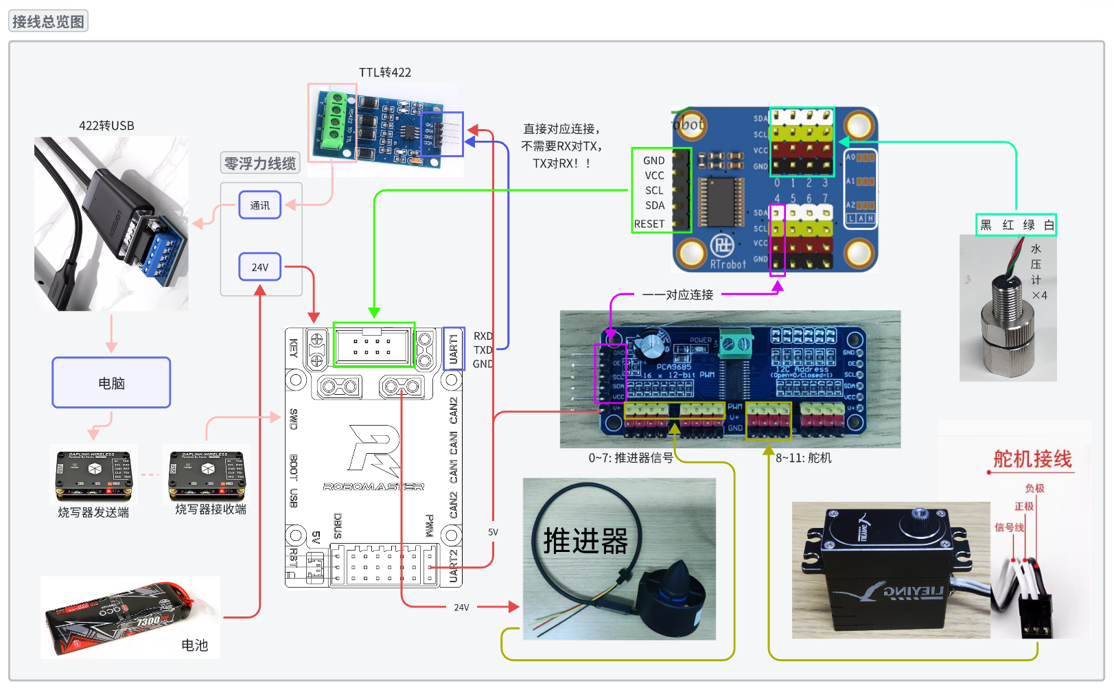
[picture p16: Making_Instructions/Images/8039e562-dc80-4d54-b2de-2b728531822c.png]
Wire_in


### Internal Wiring
C-board to I2C Expansion Board: Pins 2, 4, 6, and 8 of the IIC interface on the C-board are connected to GND, VCC, SCL, and SDA of the input terminal on the I2C expansion board (the side with 5 black base pins arranged in a row), respectively.

C板接IIC扩展板：C板IIC接口的2、4、6、8号分别与IIC扩展板输入端（一侧并排5个黑色底座针脚）的GND、VCC、SCL、SDA相连


I2C Expansion Board to Water Pressure Gauges: The GND, VCC, SCL and SDA of Ports 0 to 3 on the output terminal of the I2C Expansion Board (each port corresponding to 4 base pins of different colors arranged in a row) are connected to the black, red, green and white wires of the 4 water pressure gauges respectively.

IIC扩展板接水压计：IIC扩展板输出端0-3号端口（每个端口对应并排4个底座颜色不同的针脚）的GND、VCC、SCL、SDA分别与4个水压计的黑色、红色、绿色、白色线相连

I2C Expansion Board to PWM Expansion Board: The GND, VCC, SCL and SDA of Port 4 on the output terminal of the I2C Expansion Board are connected to the GND, VCC, SCL and SDA of the input terminal on the PWM Expansion Board (the side with 6 black base pins arranged in a row) respectively.

IIC扩展板接PWM扩展板：IIC扩展板输出端4号端口的GND、VCC、SCL、SDA分别与PWM扩展板输入端（一侧并排6个黑色底座针脚）的GND、VCC、SCL、SDA相连



C-board to PWM Expansion Board: Any 5V port of the PWM interface on the C-board is connected to the V+ of the input terminal on the PWM Expansion Board.

C板接PWM扩展板：C板PWM接口的任意一个5V端口与PWM扩展板输入端的V+相连



### Inside/Outside Devices Connection
Manual soldering is overly complex due to numerous wirings, so the following terminal blocks are provided for easy wiring.

防水舱内与舱外设备：由于接线数量较多，如果手动焊接会非常复杂，因此配置了如下的接线端子，方便接线。

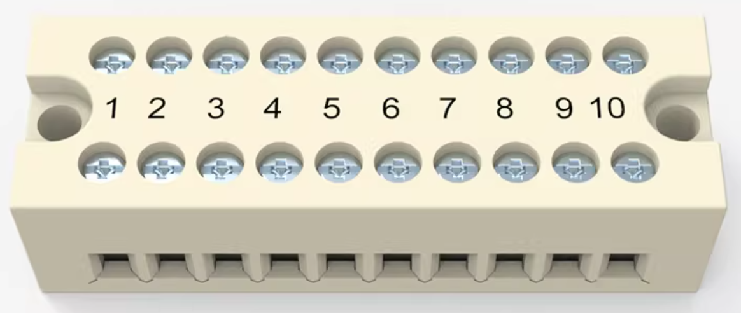
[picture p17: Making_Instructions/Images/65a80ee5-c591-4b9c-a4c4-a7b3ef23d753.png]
Terminal_block


Power Supply to C-board and Propellers: The external battery is connected to the power input port (No.8) of the internal C-board via a power cable, and any of the power output ports (No.9) on the C-board is connected to the power input ports of the 8 propellers (in parallel) through a terminal block.

电源接C板和推进器：舱外电池通过电源线连接舱内C板电源输入端（8号），C板电源输出端（9号任意一个）通过极限段子连接8个推进器电源输入端（并联）



C-board to Programmer: The wireless programmer is connected to the host computer for firmware programming and debugging.The exterior cabin wireless programmer connects to the interior cabin wireless programmer via the SWD download port on the C‑Board, with SWCLK, SWDIO, GND, and 3.3V pins connected correspondingly.

C板接烧写器：无线烧写器连接上位机，用于程序烧写、调试.  舱外无线烧写器连接舱内舱内无线烧写器，通过C板SWD下载线端口，SWCLK、SWDIO、GND、3.3V对应连接

C-board to Serial Port: The UART6 interface of the C‑Board is connected to the host computer via a TTL‑to‑422 module and a 422‑to‑USB module, for command transmission and reception.

C板接串口：C板UART6接口通过TTL转422模块、422转USB模块连接上位机，用于收发指令。

Propellers to PWM Expansion Board: The signal input terminals of the 8 external propellers are connected respectively to the PWM terminals (yellow base pins) of Ports 0 to 7 on the output terminal of the internal PWM Expansion Board.

推进器接PWM扩展板：舱外8个推进器信号输入端分别连接舱内PWM扩展板输出端0-7号端口PWM端（黄色底座针脚）。

Servos to PWM Expansion Board: The 4 external servos are connected to Ports 8 to 11 on the output terminal of the internal PWM Expansion Board respectively, with the negative poles connected to GND, the positive poles connected to V+, and the signal wires connected to PWM.

舵机接PWM扩展板：舱外4个舵机分别连接舱内PWM扩展板输出端8-11号端口，负极接GND，正极接V+，信号线接PWM。

Water Pressure Gauges to Water Pressure Gauge Adapter Boards: The 4 external water pressure gauges connect to the 4 internal water pressure gauge adapter boards, which can be directly inserted into the terminals.

水压计接水压计转接板：舱外4个水压计连接舱内4个水压机转接板，直接插入端子即可。

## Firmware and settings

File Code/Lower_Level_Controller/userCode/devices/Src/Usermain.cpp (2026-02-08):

//
// Created by LEGION on 2021/10/4.
//
//This file contains the main function and the interrupt service routines (ISRs).
//The usage of each module follows three steps: initialization, data acquisition, and execution.
//Initialization and execution are performed within the timer interrupt routine.
//Serial (UART) data reception is handled within the UART interrupt routine.
//
//此文件为主函数和中断服务函数所在地
//每个元件的使用包含三个步骤，初始化、获取数据、执行
//初始化和执行在定时器中断函数进行
//获取串口数据在串口中断函数进行
#include "Usermain.h"
#include "IMU.h"
#include "Propeller.h"
#include "Servo.h"
#include "Sensor.h"
#include "Legacy.h"
#include "Watchdog.h"
#include "LED.h"
#include "Buzzer.h"
#include "gpio.h"
#include "UART_Base.h"


//Adjust according to the vehicle version: V30, V31, V32, V33, V40.
//根据潜器版本调整，V30，V31，V32，V33，V40
VERSION_E Robot_Version = V33;


// Statically instantiated objects.
// 静态实例化对象
// IMU imu;
static Servo servo;
static Servo_I2C servo_i2c;
static Propeller_I2C propeller_i2c;
static Sonar sonar;
static Watchdog watchdog;
static LED led;
static Buzzer buzzer;


// Array of device pointers for unified management and invocation of device operations.
// ------ TODO: Select the required devices.
// 设备指针数组，用于统一管理和调用设备操作
//------TODO:选用需要的设备
static Device *device[] = {
        &IMU::imu,                         //IMU 
        &PressureSensor::pressure_sensor,  //Pressure Sensor 水压计
        &propeller_i2c,                    //Propeller（PWM control via the PWM expansion board） 推进器（PWM扩展板控制）
        //&propeller,                      //Propeller（PWM control via the Robomaster_C board） 推进器（C板PWM控制）
				&servo_i2c,                        //Servo（PWM control via the PWM expansion board） 舵机（PWM扩展板控制）
				//&servo,                          //Servo（PWM control via the Robomaster_C board） 舵机（C板PWM控制）
        //&watchdog,                       //Watchdog 窗口看门狗
        &led,                              //LED
        //&buzzer                          //Buzzer 蜂鸣器
};

// Macro definition for the number of devices.
// 定义设备数量宏
#define DEVICE_NUM (sizeof(device) / sizeof(device[0]))

volatile bool system_init_flag = false;
volatile bool tick_300hz = false;
uint8_t RxBuffer[SERIAL_LENGTH_MAX] = {0};
volatile uint8_t key_raw_state = 1;
uint32_t key_last_stamp;
volatile int32_t time_start = 0, time_end = 0, time_interval = 0, cnt = 0;

// Timer interrupt service routine (ISR) for periodic device processing.
// 定时器中断服务函数, 用于周期性处理设备
void HAL_TIM_PeriodElapsedCallback(TIM_HandleTypeDef *htim)
{
    if(!system_init_flag) return;
    if(htim == &htim1){ //300Hz
        tick_300hz = true;
    }
}

// UART receive interrupt service routine (ISR) for handling device-specific UART reception tasks.
// 串口接收中断服务函数, 用于处理设备的串口接收任务
void HAL_UARTEx_RxEventCallback(UART_HandleTypeDef *huart, uint16_t datasize)//HAL_UART_RxCpltCallback
{
    if(huart->Instance==USART6) {
        // if (datasize >= 2){
            // if (strncmp((char *)RxBuffer, "IM", 2) == 0)
            //     device[0]->Receive();
            // else if (strncmp((char *)RxBuffer, "PS", 2) == 0)
            //     device[1]->Receive();
            // else if (strncmp((char *)RxBuffer, "PR", 2) == 0)
            //     device[2]->Receive();
            // else if (strncmp((char *)RxBuffer, "SE", 2) == 0)
            //     device[3]->Receive();
            // else if (strncmp((char *)RxBuffer, "LE", 2) == 0)
            //     device[4]->Receive();
            for(int i=0;i<DEVICE_NUM;++i){
                device[i]->Receive();
            // }
        }
        
        std::memset(RxBuffer, 0, SERIAL_LENGTH_MAX);
        // Re-enable UART reception.
				// 重新开启接收
        HAL_UARTEx_ReceiveToIdle_IT(&huart6, RxBuffer, SERIAL_LENGTH_MAX);
    }
}

// UART transmit interrupt callback function.
// 串口发送中断回调函数
void HAL_UART_TxCpltCallback(UART_HandleTypeDef *huart) {
    #define HANDLE_UART_TX(ID)                            \
        do {                                              \
            if (huart == uartHandleList[ID]) {            \
                UARTBaseLite<ID>::GetInstance().OnTxDone(); \
                return;                                   \
            }                                             \
        } while (0)

    HANDLE_UART_TX(1);
    HANDLE_UART_TX(6);

    #undef HANDLE_UART_TX
    // if(huart == &huart1) {
    //     UARTBaseLite<1>::GetInstance().OnTxDone();
    // }
    // else if(huart == &huart6){
    //     UARTBaseLite<6>::GetInstance().OnTxDone();
    // }
}

// Key/button interrupt (currently unused).
// 按键中断，暂时无用
// void HAL_GPIO_EXTI_Callback(uint16_t GPIO_Pin){
//     if(system_init_flag == 0)return;
//     if (GPIO_Pin == GPIO_PIN_0){
//         key_raw_state = HAL_GPIO_ReadPin(KEY_GPIO_Port,KEY_Pin);
//         uint32_t time_interval = HAL_GetTick() - key_last_stamp;
//         key_last_stamp = HAL_GetTick();
//         /*if (time_interval >= 50){
//             if (key_raw_state == 1){
//                 period = 5000;
//             }else{
//                 period = 500;
//             }
//         }*/
//     }
//     IMU::imu.ITHandle(GPIO_Pin);
// }

/**
  * @brief  The application entry point.
  * @retval int
  */
// Entry point of the main function.
// 主函数入口
int main(void)
{
    /* MCU Configuration--------------------------------------------------------*/

    /* Reset of all peripherals, Initializes the Flash interface and the Systick. */
    HAL_Init();

    /* Configure the system clock */
    SystemClock_Config();

    /* Initialize all configured peripherals */
    MX_GPIO_Init();
    MX_DMA_Init();
    MX_TIM5_Init();
    MX_TIM1_Init();
    MX_TIM4_Init();
    MX_TIM6_Init();
    MX_TIM7_Init();
    MX_TIM10_Init();
    MX_TIM8_Init();
    MX_ADC1_Init();
    MX_ADC3_Init();
    MX_USART1_UART_Init();
    MX_USART6_UART_Init();
    MX_USART3_UART_Init();
    MX_CAN1_Init();
    MX_CAN2_Init();
    MX_I2C2_Init();
    MX_I2C3_Init();
    MX_SPI1_Init();
    MX_SPI2_Init();
    //MX_IWDG_Init();
    MX_USB_DEVICE_Init();

    HAL_TIM_Base_Start_IT(&htim5);
    HAL_TIM_Base_Start_IT(&htim1);
    HAL_TIM_PWM_Start_IT(&htim1, TIM_CHANNEL_1);
    HAL_TIM_PWM_Start_IT(&htim1, TIM_CHANNEL_2);
    HAL_TIM_PWM_Start_IT(&htim1, TIM_CHANNEL_3);
    HAL_TIM_PWM_Start_IT(&htim1, TIM_CHANNEL_4);


    HAL_TIM_Base_Start_IT(&htim8);
    HAL_TIM_PWM_Start_IT(&htim8, TIM_CHANNEL_1);
    HAL_TIM_PWM_Start_IT(&htim8, TIM_CHANNEL_2);
    HAL_TIM_PWM_Start_IT(&htim8, TIM_CHANNEL_3);
    //TODO adc校准？
    //RemoteControl::init();
    bsp_flash_read(&flashData);
    HAL_TIM_Base_Start_IT(&htim10);
    HAL_TIM_PWM_Start_IT(&htim10, TIM_CHANNEL_1);
    HAL_TIM_Base_Start_IT(&htim6);
    HAL_TIM_Base_Start_IT(&htim7);

		// Initialize all devices.
    // 初始化所有设备
    for(int i = 0; i < DEVICE_NUM; ++i){
        device[i] -> Init();
    }
		
		// Set the initialization-complete flag.
    // 设置初始化完成标志
    system_init_flag = true;
    time_start = HAL_GetTick();

    while (1){
        // time_start = HAL_GetTick();
        if(tick_300hz){
            tick_300hz = false;
            static int a = 0;
            a++;
            for(int i = 0 ; i < DEVICE_NUM ; ++i){
                device[i]->Handle();
//                if (a==150&&i==4)
//                {
//                    time_end = HAL_GetTick();
//                    time_interval = time_end - time_start;
//                    send_int(time_interval, 1);
//                    a = 0;
//                    time_start = HAL_GetTick();
//                }
            }
            
        }
    }
}

void send_float(float value, uint8_t decimalPlaces, bool endSign){
    bool isNegative = 0;
    uint8_t len = 0;
    static char buffer_float[20] = {0};
		
		// Handle negative values.
    // 处理负数
    if(value < 0){
        isNegative = 1;
        value = -value;
    }
    if(isNegative) {
        buffer_float[0] = '-';
        len = 1;
    }

		// Convert the integer part.
    // 转换整数部分
    int32_t intPart = (int)value;
    len += sprintf(buffer_float+len, "%d", intPart);
		
		// Process the fractional part.
    // 处理小数部分
    if (decimalPlaces > 0) {
        buffer_float[len++] = '.';

        float fraction = value - (float)intPart;
        for (uint8_t i = 0; i < decimalPlaces; i++) {
            fraction *= 10;
            int digit = (int)fraction;
            buffer_float[len++] = digit + '0';
            fraction -= digit;
        }
    }

		// If this is the final element, append a newline; otherwise, append a comma.
    // 若结束则换行，否则是逗号
    if(endSign)
        buffer_float[len++] = '\n'; // Null terminator of the string 字符串结束符
    else
        buffer_float[len++] = ',';

    buffer_float[len] = '\0';

    // HAL_UART_Transmit(&huart6, (uint8_t *)buffer, len, 0x00ff);
    UARTBaseLite<6>::GetInstance().Transmit(reinterpret_cast<uint8_t *>(buffer_float),len);
}

void send_int(int32_t value, bool endSign){
    static char buffer_int[20] = {0};
    uint8_t len = 0;
    bool isNegative = 0;

		// Handle negative values.
    // 处理负数
    if(value < 0){
        isNegative = 1;
        value = -value;
    }
    if(isNegative) {
        buffer_int[0] = '-';
        len = 1;
    }

    len += sprintf(buffer_int+len, "%d", value);

    if(endSign)
        buffer_int[len++] = '\n';
    else
        buffer_int[len++] = ',';

    buffer_int[len] = '\0';
    // HAL_UART_Transmit(&huart6, (uint8_t *)buffer, len, 0x00ff);
    UARTBaseLite<6>::GetInstance().Transmit(reinterpret_cast<uint8_t *>(buffer_int),len);
}

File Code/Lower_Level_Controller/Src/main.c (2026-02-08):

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
/* Includes ------------------------------------------------------------------*/
#include "main.h"
#include "adc.h"
#include "can.h"
#include "dma.h"
#include "i2c.h"
#include "iwdg.h"
#include "spi.h"
#include "tim.h"
#include "usart.h"
#include "usb_device.h"
#include "gpio.h"

/* USER CODE BEGIN Includes */
#include <stdarg.h>
#include <string.h>
#include <math.h>
#include <stdio.h>
#include "usbd_cdc_if.h"
/* USER CODE END Includes */

/* USER CODE BEGIN PTD */
/*******************************************************************************
* Copyright (c) 2025.
 * IWIN-FINS Lab, Shanghai Jiao Tong University, Shanghai, China.
 * All rights reserved.
 ******************************************************************************/

#if __ARMCC_VERSION >= 6000000
__asm(".global __use_no_semihosting");
#elif __ARMCC_VERSION >= 5000000
#pragma import(__use_no_semihosting)
#else
#error Unsupported compiler
#endif

#include <rt_sys.h>
#include <rt_misc.h>
#include <time.h>

const char __stdin_name[] =  ":tt";
const char __stdout_name[] =  ":tt";
const char __stderr_name[] =  ":tt";

FILEHANDLE _sys_open(const char *name, int openmode){
    return 1;
}

int _sys_close(FILEHANDLE fh){
    return 0;
}

char *_sys_command_string(char *cmd, int len){
    return NULL;
}

int _sys_write(FILEHANDLE fh, const unsigned char *buf, unsigned len, int mode){
    return 0;
}

int _sys_read(FILEHANDLE fh, unsigned char *buf, unsigned len, int mode){
    return -1;
}

void _ttywrch(int ch){
}

int _sys_istty(FILEHANDLE fh){
    return 0;
}

int _sys_seek(FILEHANDLE fh, long pos){
    return -1;
}

long _sys_flen(FILEHANDLE fh){
    return -1;
}

void _sys_exit(int return_code) {
    while (1)
        ;
}

clock_t clock(void){
    clock_t tmp;
    return tmp;
}

void _clock_init(void){
}

time_t time(time_t *timer){
    time_t tmp;
    return tmp;
}

int system(const char *string){
    return 0;
}

/* USER CODE END PTD */


void SystemClock_Config(void);
/**
  * @brief  The application entry point.
  * @retval int
  */


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


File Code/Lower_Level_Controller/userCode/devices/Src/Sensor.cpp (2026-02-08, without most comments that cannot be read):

#include "Sensor.h"
#include "Kalman_filter.h"

extern I2C_HandleTypeDef hi2c2;

PressureSensor PressureSensor::pressure_sensor;

KalmanFilter Pressure_Kf[4] = {KalmanFilter(0.01, 0.05, 1.0, 0.0),
                               KalmanFilter(0.01, 0.05, 1.0, 0.0),
                               KalmanFilter(0.01, 0.05, 1.0, 0.0),
                               KalmanFilter(0.01, 0.05, 1.0, 0.0)};

void PressureSensor::Init()
{

		// ------ TODO: 3D coordinates of the four pressure sensors. These values must be obtained via measurement and updated accordingly.
    //------TODO:4个水压计三维坐标，由测量得到，需要修改
    Sensor_Site_t _site = {
        .x = {-12, 12, 12, -12},
        .y = {-5.4, -5.4, 5.4, 5.4},
        .z = {0, 0, 0, 0}
        /*.x={0},
        .y={1},
        .z={2},*/
    };
    site = _site;

    CurrentID = 0;

    // flag_Busy = 0;

    bsp_flash_read(&flashData);

    for (int i = 0; i < SENSOR_NUM; ++i)
    {
        TCA_SetChannel(i);
        HAL_Delay(5);
        Init_single(i);
    }

    data_plane[0] = 0;
    data_plane[1] = 0;
    data_plane[2] = 1;
    data_plane[3] = 0;
    data_plane[4] = 0;

    flag_calibrate = false;
    flag_read_pres = false;

    /*quat[0]=1.0f;
    quat[1]=0.0f;
    quat[2]=0.0f;
    quat[3]=0.0f;
*/
}

void PressureSensor::Handle()
{
    // if(tim_id == 1){
    // flag_Busy = 1;

    if (flag_calibrate)
    {
        Calibrate(); // Calibration 校准
        flag_calibrate = false;
    }
    else
    {
        Handle_all();
    }
    /*
    Update_plane();//计算机器人参考系下水面方程
    data_depth=-data_plane[3];//计算深度
    pitch=atan(-data_plane[0]/(sqrt(data_plane[1]*data_plane[1]+data_plane[2]*data_plane[2])));//计算俯仰角
    roll=atan(data_plane[1]/data_plane[2]);//计算横滚角
     */
    data_depth = (data_pressure[3] + data_pressure[2] + data_pressure[1] + data_pressure[0]) / 4;
    data_roll = data_pressure[0] + data_pressure[1] - data_pressure[2] - data_pressure[3];
    data_pitch = data_pressure[0] + data_pressure[3] - data_pressure[1] - data_pressure[2];
}

void PressureSensor::Receive()
{
    if (strncmp((char *)RxBuffer, "CA", 2) == 0)
    {
        flag_calibrate = true;
    }
    else if (strncmp((char *)RxBuffer, "VA", 2) == 0)
    {
        flag_read_pres = true;
    }
}

void PressureSensor::Delay_us(uint32_t us)
{
    uint32_t i;
    for (i = 0; i < us; i++)
    {
        int a = 10; // delay based on main clock, 168Mhz
        while (a--);
    }
}

unsigned char PressureSensor::MS5837_30BA_Crc4(int id)
{
    int cnt;
    int t;
    unsigned int n_rem = 0;
    unsigned char n_bit;
    unsigned char a = 0;
    unsigned char b = 0;
    unsigned short int n_prom[8];

    for (t = 0; t < 7; t++)
    {
        n_prom[t] = Cal_C[id][t];
    }
    n_prom[0] = ((n_prom[0]) & 0x0FFF);
    n_prom[7] = 0;
    for (cnt = 0; cnt < 16; cnt++)
    {
        if (cnt % 2 == 1)
            n_rem ^= (unsigned short)((n_prom[cnt >> 1]) & 0x00FF);
        else
            n_rem ^= (unsigned short)(n_prom[cnt >> 1] >> 8);
        for (n_bit = 8; n_bit > 0; n_bit--)
        {
            if (n_rem & (0x8000))
                n_rem = (n_rem << 1) ^ 0x3000;
            else
                n_rem = (n_rem << 1);
        }
    }
    n_rem = ((n_rem >> 12) & 0x000F);
    a = (n_rem ^ 0x00);
    b = Cal_C[id][0] >> 12;
    if (a == b)
    {
        return 1;
    }
    else
        return 0;
}

void PressureSensor::MS5837_30BA_ReSet(void)
{
    uint8_t data[1];
    data[0] = MS5837_30BA_ResetCommand;
    HAL_I2C_Master_Transmit(&hi2c2, B02_IIC_ADDRESS, data, 1, 0xffff);
}

uint8_t PressureSensor::MS5837_30BA_PROM(int id)
{
    uint8_t memaddr[1];
    uint8_t data[2];
    int i;

    MS5837_30BA_ReSet();
    HAL_Delay(20);
    for (i = 0; i < 7; i++)
    {
        memaddr[0] = MS5837_30BA_PROM_RD + (i * 2);
        HAL_I2C_Master_Transmit(&hi2c2, B02_IIC_ADDRESS, memaddr, 1, 0xffff);
        HAL_I2C_Master_Receive(&hi2c2, B02_IIC_ADDRESS, data, 2, 0xffff);
        Cal_C[id][i] = (((uint16_t)data[0] << 8) | data[1]);
    }
    return !Cal_C[id][0];
}

unsigned long PressureSensor::MS5837_30BA_GetConversion(uint8_t command)
{
    unsigned long conversion = 0;
    uint8_t data = MS5837_30BA_ADC_RD;
    uint8_t temp[3];
    HAL_I2C_Master_Transmit(&hi2c2, B02_IIC_ADDRESS, &command, 1, 0xffff);
    HAL_Delay(2);
    // Delay_us(15000);
    HAL_I2C_Master_Transmit(&hi2c2, B02_IIC_ADDRESS, &data, 1, 0xffff);

    HAL_I2C_Master_Receive(&hi2c2, B02_IIC_ADDRESS, temp, 3, 0xffff);
    conversion = (unsigned long)temp[0] * 65536 + (unsigned long)temp[1] * 256 + (unsigned long)temp[2];
    return conversion;
}

/*signed int PressureSensor::MS5837_30BA_GetTemp(int id)
{
    if(flag_ok[id]) {
        D2_Temp = MS5837_30BA_GetConversion(MS5837_30BA_D2_OSR_8192);
        HAL_Delay(20);
        dT = D2_Temp - (((uint32_t) Cal_C[id][5]) * 256l);
        return dT;
    }
    else return -1;
}*/

float PressureSensor::MS5837_30BA_GetData(int id)
{

    if (flag_ok[id])
    {
        D2_Temp = MS5837_30BA_GetConversion(MS5837_30BA_D2_OSR1024);
        // HAL_Delay(1);
        // Delay_us(30000);
        D1_Pres = MS5837_30BA_GetConversion(MS5837_30BA_D1_OSR1024);
        // HAL_Delay(3);
        // Delay_us(30000);
        dT = D2_Temp - (((uint32_t)Cal_C[id][5]) * 256l);
        SENS = (int64_t)Cal_C[id][1] * 65536l + ((int64_t)Cal_C[id][3] * dT) / 128l;
        OFF_ = (int64_t)Cal_C[id][2] * 131072l + ((int64_t)Cal_C[id][4] * dT) / 64l;

        TEMP = 2000l + (int64_t)(dT)*Cal_C[id][6] / 8388608LL;


        if (TEMP < 2000) // low temp
        {

            Ti = (11 * (int64_t)(dT) * (int64_t)(dT) / (34359738368LL));
            OFFi = (31 * (TEMP - 2000) * (TEMP - 2000)) / 8;
            SENSi = (63 * (TEMP - 2000) * (TEMP - 2000)) / 32;
        }
        else
        { // high temp
            Ti = 2 * (dT * dT) / (137438953472LL);
            OFFi = (1 * (TEMP - 2000) * (TEMP - 2000)) / 16;
            SENSi = 0;
        }
        OFF2 = OFF_ - OFFi;
        SENS2 = SENS - SENSi;
        /*if(D1_Pres==0||D2_Temp==0) return last_measure[id];
        else{
            float pressure = ((D1_Pres * SENS2) / 2097152.0 - OFF2) / 32768.0 / 100.0;
            last_measure[id]=pressure;
            return pressure;

        }*/
        float pressure = ((D1_Pres * SENS2) / 2097152.0 - OFF2) / 32768.0 / 100.0;
        return pressure;




    }
    else
        return -1;
}
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

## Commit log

2026-01-31 feat: update structure model
    [9-16-2.stp.STEP, CNC_Maching.xlsx, CNC加工.xlsx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]
2026-02-08 Update the BOM
    [BOM.xlsx]

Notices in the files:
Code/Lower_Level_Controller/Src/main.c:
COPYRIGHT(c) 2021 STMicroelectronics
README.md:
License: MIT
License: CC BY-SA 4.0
